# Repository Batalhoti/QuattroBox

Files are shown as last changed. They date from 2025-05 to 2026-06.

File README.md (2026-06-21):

# QuattroBox

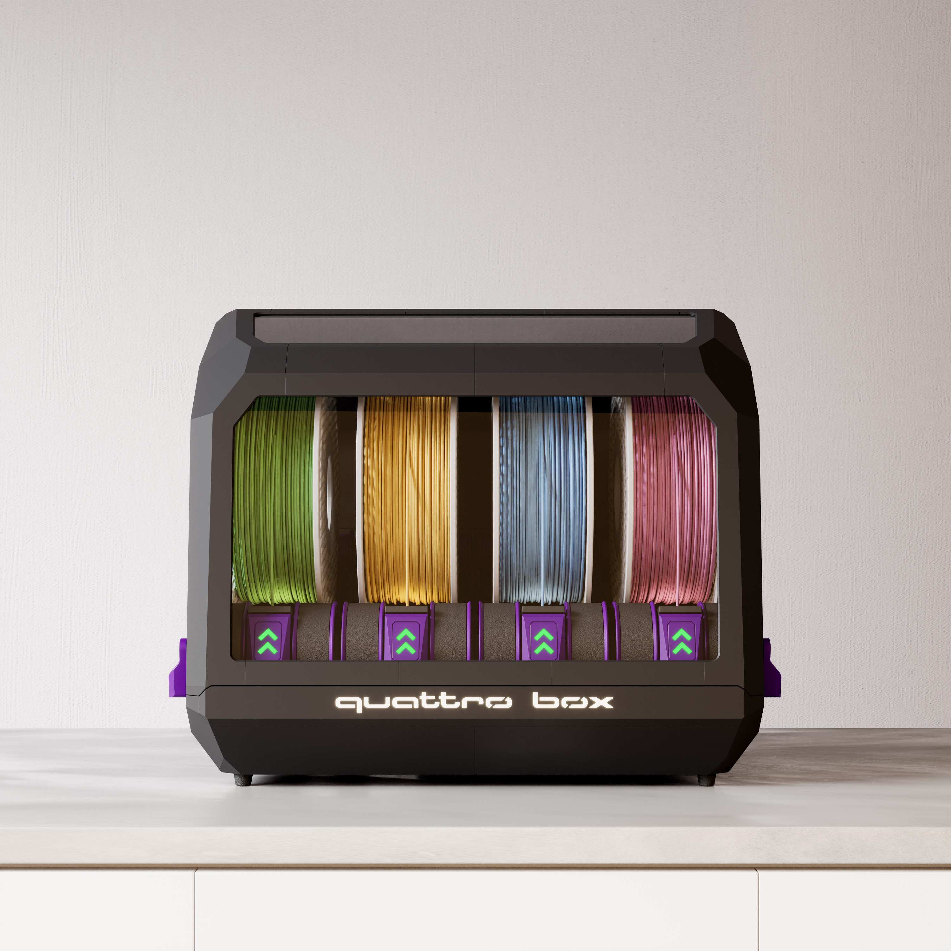
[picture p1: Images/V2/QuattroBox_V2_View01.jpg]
<p align="center">
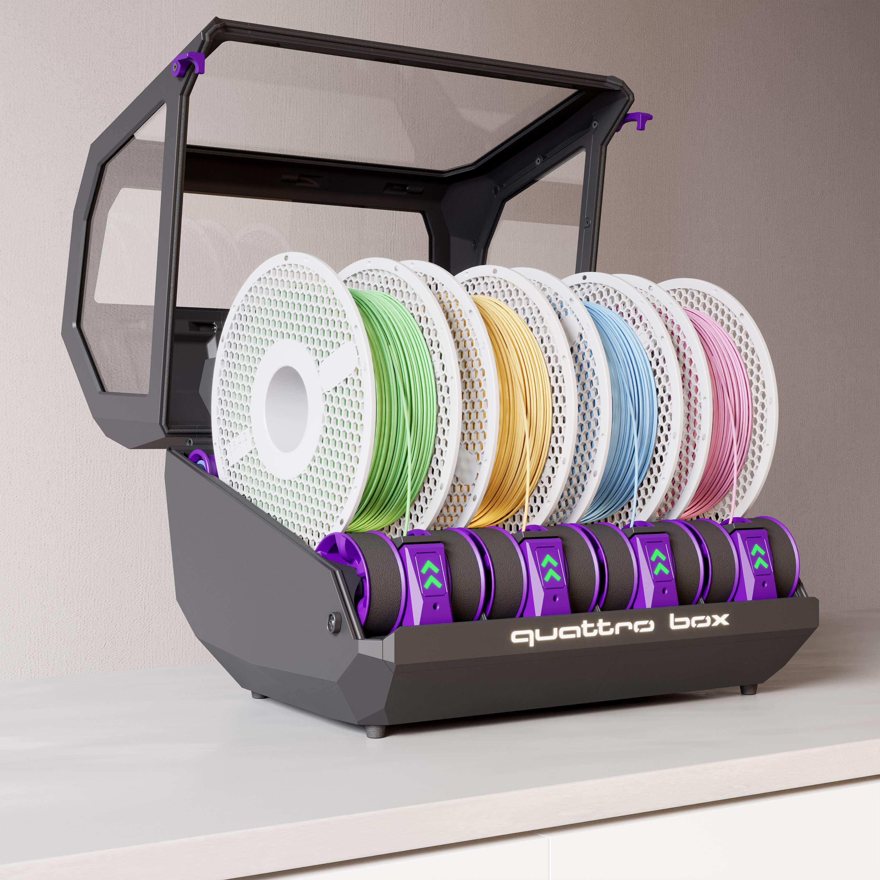
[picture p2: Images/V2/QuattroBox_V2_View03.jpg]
<p align="center">
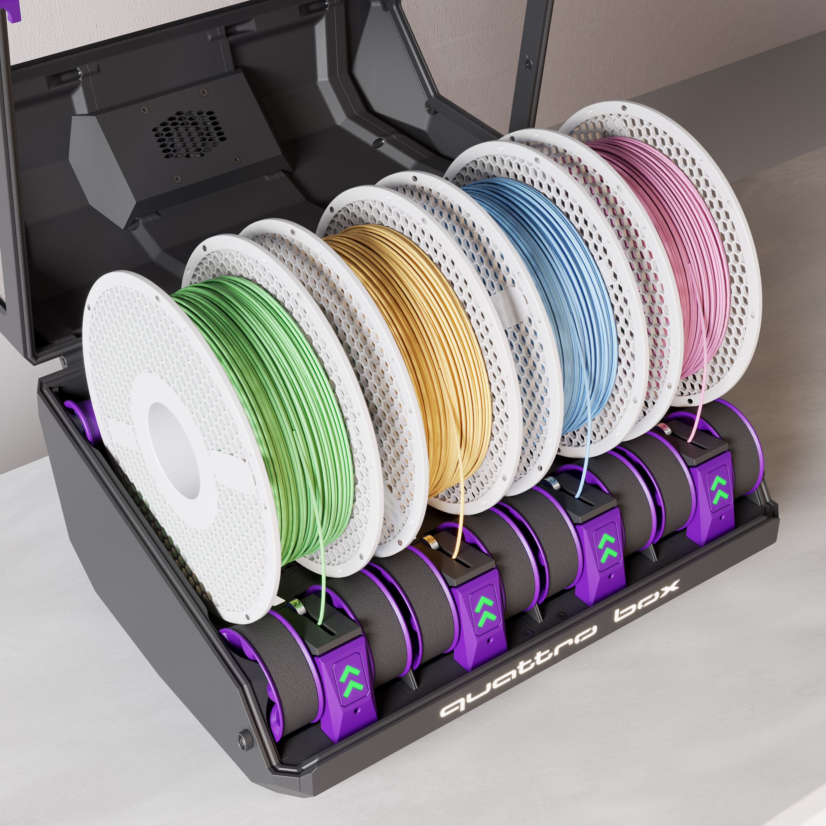
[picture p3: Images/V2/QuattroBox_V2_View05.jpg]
<p align="center">

## Description

QuattroBox v2 is the complete evolution of my MMU for 3D printers.
This version has been fully redesigned from the ground up, focusing on simplicity, compactness, and everyday usability.

I kept as much compatibility as possible with components from the previous version, while introducing significant improvements in both mechanical design and overall user experience.

## Key features
- Integrated filament dryer with AC heater
- Exhaust system for moisture removal
- Dedicated 4A power supply (optional)
- More compact extruder using a 23 mm NEMA17 (pancake)
- Hub with integrated Sync PSF
- Hinged lid (compatible with v1 panels)
- Magnetic bottom cover for easy access and maintenance
- Simplified and more organized assembly process
- All electronic components are assembled outside the enclosure before final installation
- Cable management clips
- Fully 3D printed structure (no aluminum extrusions required)
- Mounting supports to rest the MMU on the printer’s top extrusions
- Optimized for a 180 mm print area, with up to 142 mm height
- Compatible with [**Happy Hare**](https://github.com/moggieuk/Happy-Hare/wiki) for MMU control 

### Design and usability

The QuattroBox v2 design has also evolved significantly, not only in aesthetics but mainly in everyday usability. The status LED buttons are part of the system’s visual and functional identity, making it easy to quickly understand its operation. The system also features dedicated lighting to monitor the filament path. The internal layout has been reorganized to be cleaner and more intuitive, improving both assembly and maintenance. Access to components has also been designed to be simpler and more practical for day-to-day use.

### Design philosophy

QuattroBox v2 was designed to be accessible and easy to build, without compromising functionality.
The goal is to eliminate unnecessary complexity while maintaining a reliable and efficient multi-material system.  

##

I have a Discord channel on [HappyHare](https://discord.gg/pGSMCnBXc7), feel free to ask your questions and give suggestions

E se voce é brasileiro tenho um canal no servidor da [Orion 3D](https://discord.gg/Ap2ZFJXG7s)

## 

[BOM V2](https://docs.google.com/spreadsheets/d/1JrKG5omNthBb1Ab2Xag8QSc8Q7b502xr/edit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)

If you want to buy the complete kit

[SeleadLab v2 (Affiliate Link)](https://s.click.aliexpress.com/e/_c2JtqLK5)

[Trianglelab v2 (Affiliate Link)](https://s.click.aliexpress.com/e/_c4NRFI21)

## My build v1

[VIDEO 1](https://photos.app.goo.gl/y86quBDpxgd3wVg19)

[VIDEO 2](https://photos.app.goo.gl/qtu92ND3gbf3hNFr5)

<p align="center">
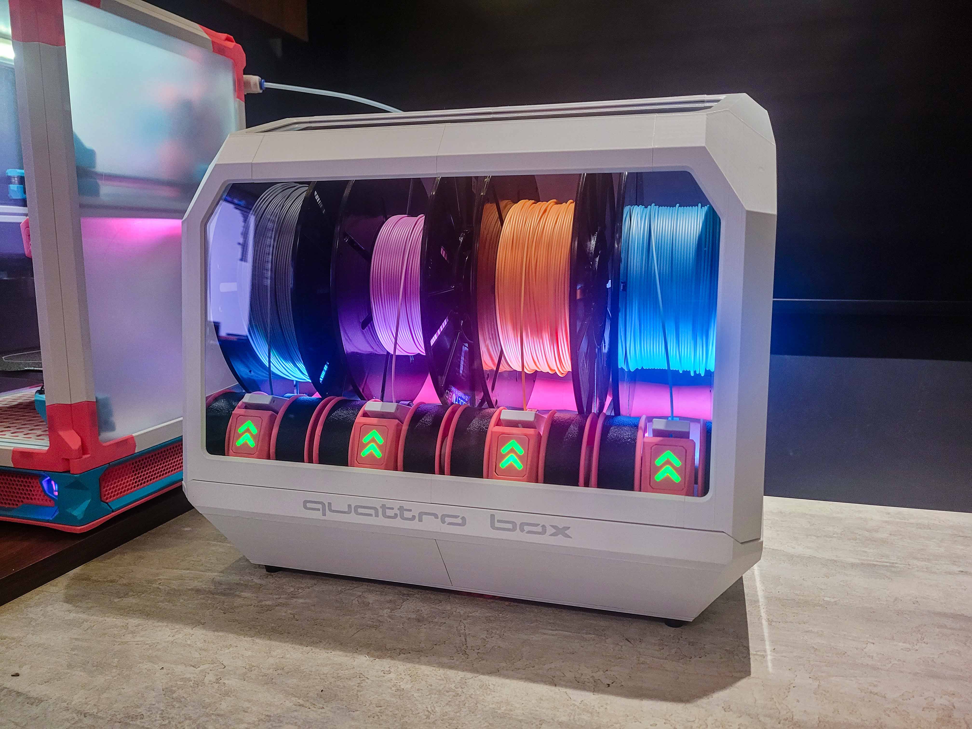
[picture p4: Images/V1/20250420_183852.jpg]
<p align="center">

## My build v2

Soon

## Acknowledgements

Special thanks to SkiBike for the [Filamentalist](https://github.com/Enraged-Rabbit-Community/ERCF_v2/tree/master/Recommended_Options/Filamentalist_Rewinder) design and to ArmoredTurtle for the [BoxTurtle](https://github.com/ArmoredTurtle/BoxTurtle) design, both of which inspired this project.
I also thank Diem who helped me with the publication here on GitHub

### [Change log](ChangeLog.md)

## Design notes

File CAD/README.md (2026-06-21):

To make the CAD model easier to navigate, the project is provided in two separate files:

### QuattroBox_V2_Assembly_up_to_180mm
Contains the larger parts split into multiple sections, allowing them to be printed on printers with a 180 mm or larger build area.

### QuattroBox_V2_Assembly_up_to_300mm

Contains the larger parts in fewer sections or as full-size parts, intended for printers with a 300 mm or larger build area.

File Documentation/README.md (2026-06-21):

I originally planned to create a step-by-step installation guide, but the release of Happy Hare V4 is approaching. For this reason, I am providing the configuration files that I currently use.

Please note that you will still need to verify and adjust the following parameters according to your setup:

- Toolhead sensor pins
- Cutter pins
- Toolhead sensor distances

It is recommended to review these settings before putting the system into operation.

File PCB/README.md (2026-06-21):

## PCBs
I am providing PCBs for the button and LED lane, making assembly easier for users who have little or no experience with wire soldering.

The PCB files are available for manufacturing. Ready-to-purchase versions are not yet available on AliExpress, but they are expected to be available soon.

### Button
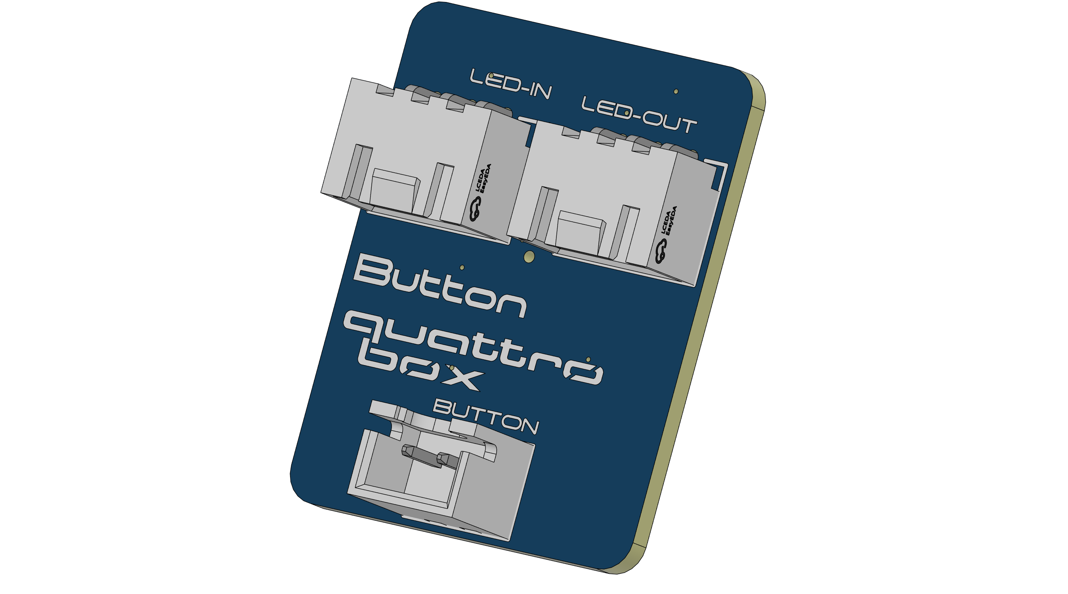
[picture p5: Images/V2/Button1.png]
<p align="center">

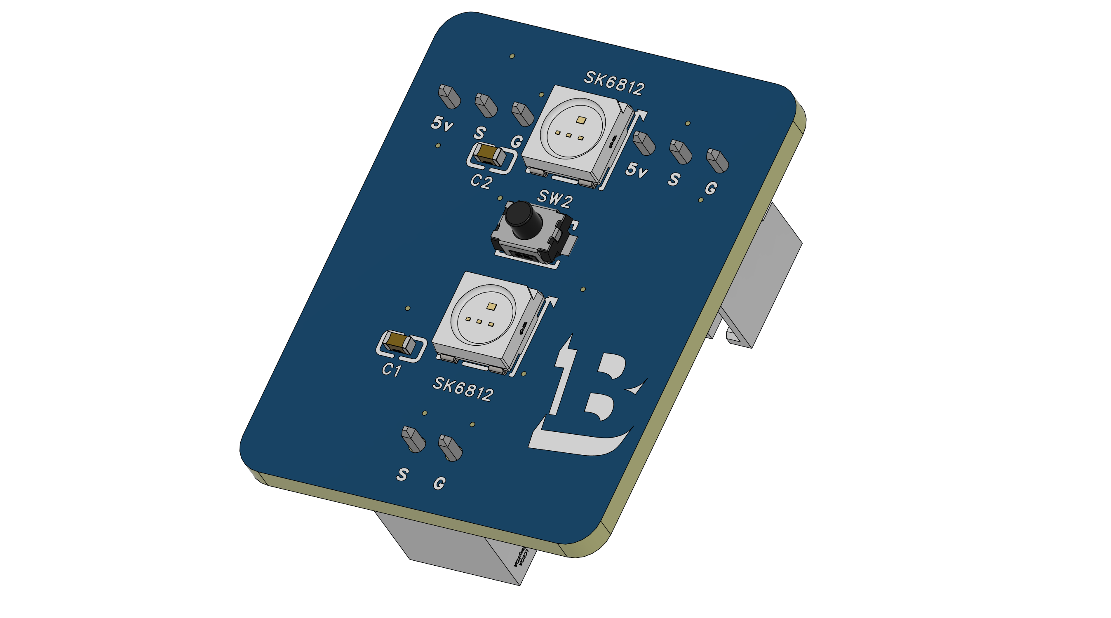
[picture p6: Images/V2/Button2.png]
<p align="center">

### LED Lane

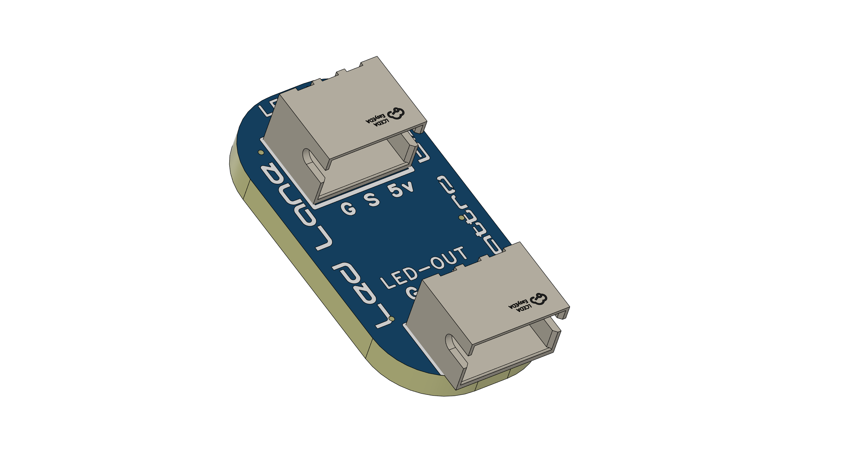
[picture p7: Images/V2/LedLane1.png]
<p align="center">

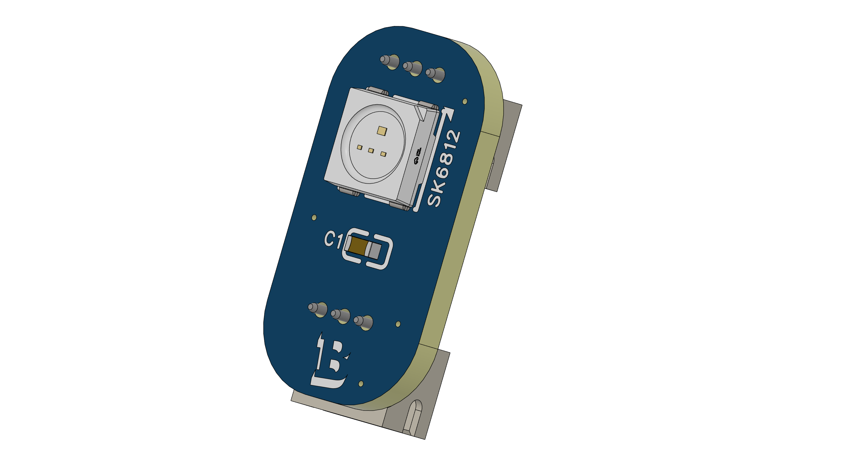
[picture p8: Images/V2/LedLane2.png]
<p align="center">

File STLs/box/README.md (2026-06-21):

### Box Single-Part 
For printers with a 400 mm or larger build volume.

### Box 2-Part 
For printers with a 300 mm or larger build volume.

### Box 8-Part 
For printers with a 180 mm or larger build volume.

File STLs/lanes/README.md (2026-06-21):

### base 1-Part 
For printers with a 300 mm or larger build volume.

### base 2-Part 
For printers with a 180 mm or larger build volume.

### PCBs Parts

If you are using the custom QuattroBox PCBs, also print the Button_PCB and LED_PCB parts

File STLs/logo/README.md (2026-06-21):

### Logo MMU
Printed as a single multicolor part and requires a printer equipped with an MMU system.
### Logo MMU 3-Part
A split version of the MMU logo designed for printers with smaller build volumes. Printed as three multicolor sections and assembled after printing. Requires an MMU system.

### Slicer MMU Logo
To print the Multi Color logo, adjust your slicer settings and enable the "Interface Shells" option under the Multimaterial section.

This setting helps improve the interface quality between different colors, resulting in a cleaner and more consistent finish.

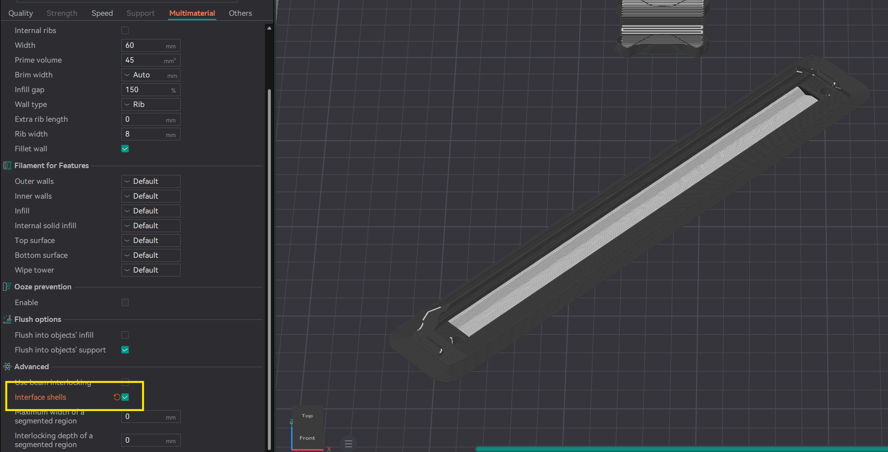
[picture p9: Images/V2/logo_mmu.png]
<p align="center">

### Logo Multi Part
Printed as separate colored parts that are assembled after printing. Does not require an MMU system.
### Logo Multi Part 3-Part
A split version of the Multi-Part logo designed for printers with smaller build volumes. Printed as three separate sections and assembled after printing. Does not require an MMU system!

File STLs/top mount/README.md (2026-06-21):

### Top Mount
For users with Voron printers that have non-standard dimensions, I am providing parametric files compatible with both the Voron and Monolith Panel standards.

Simply open the file in Fusion and modify the frame_size parameter, which represents the total outer length of the frame, measured on the outside and excluding the panels.
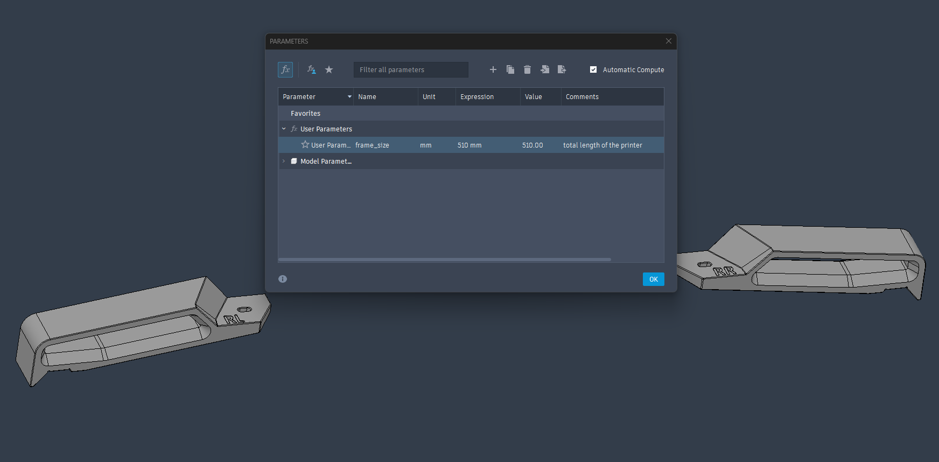
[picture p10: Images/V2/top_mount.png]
<p align="center">

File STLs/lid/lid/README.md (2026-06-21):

### Side 1-Part 
For printers with a 300 mm or larger build volume.

### Side 4-Part 
For printers with a 180 mm or larger build volume.

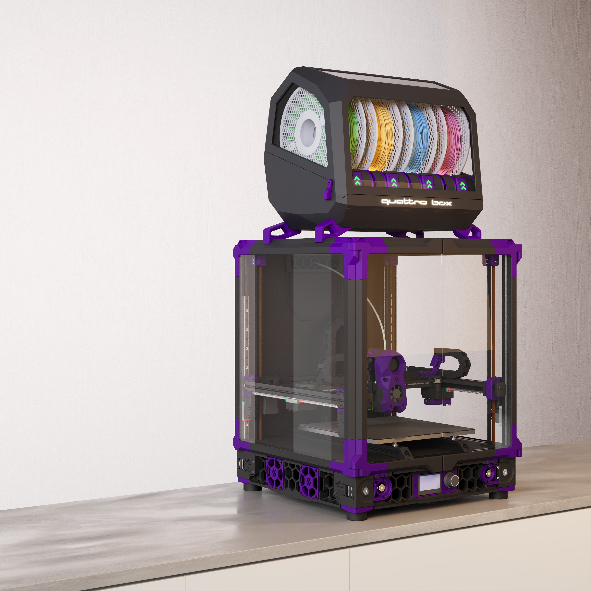
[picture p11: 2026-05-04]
Images/V2/QuattroBox_V2_V24_monolith_r1_View01.jpg

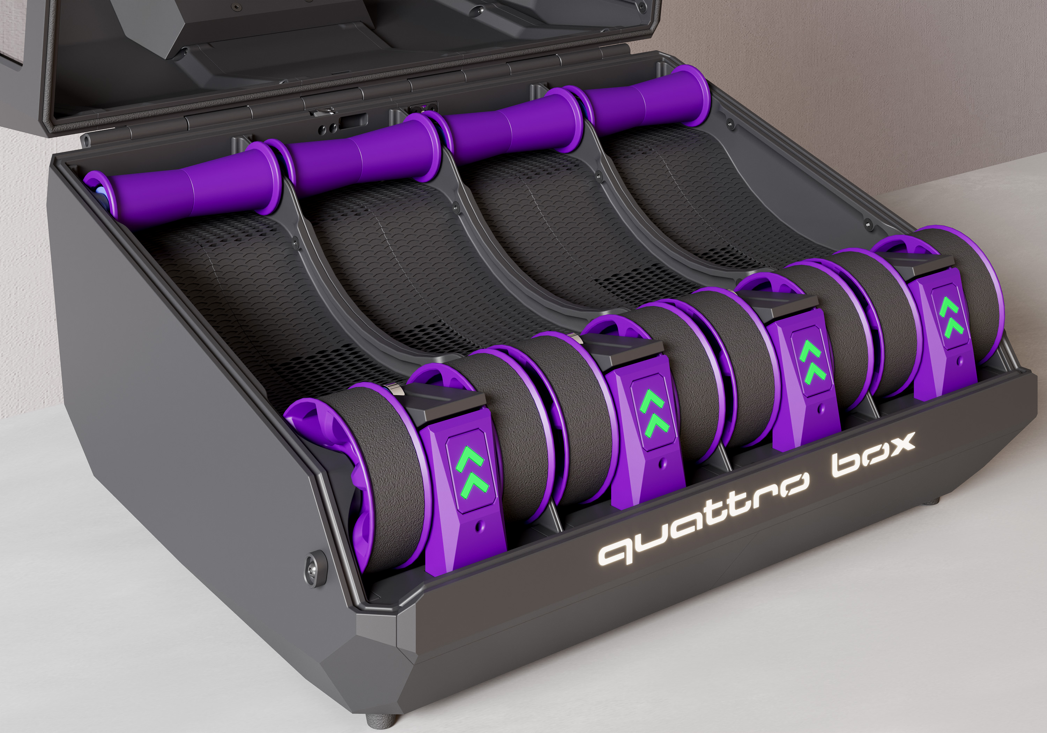
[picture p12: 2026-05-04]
Images/V2/QuattroBox_V2_View07.jpg

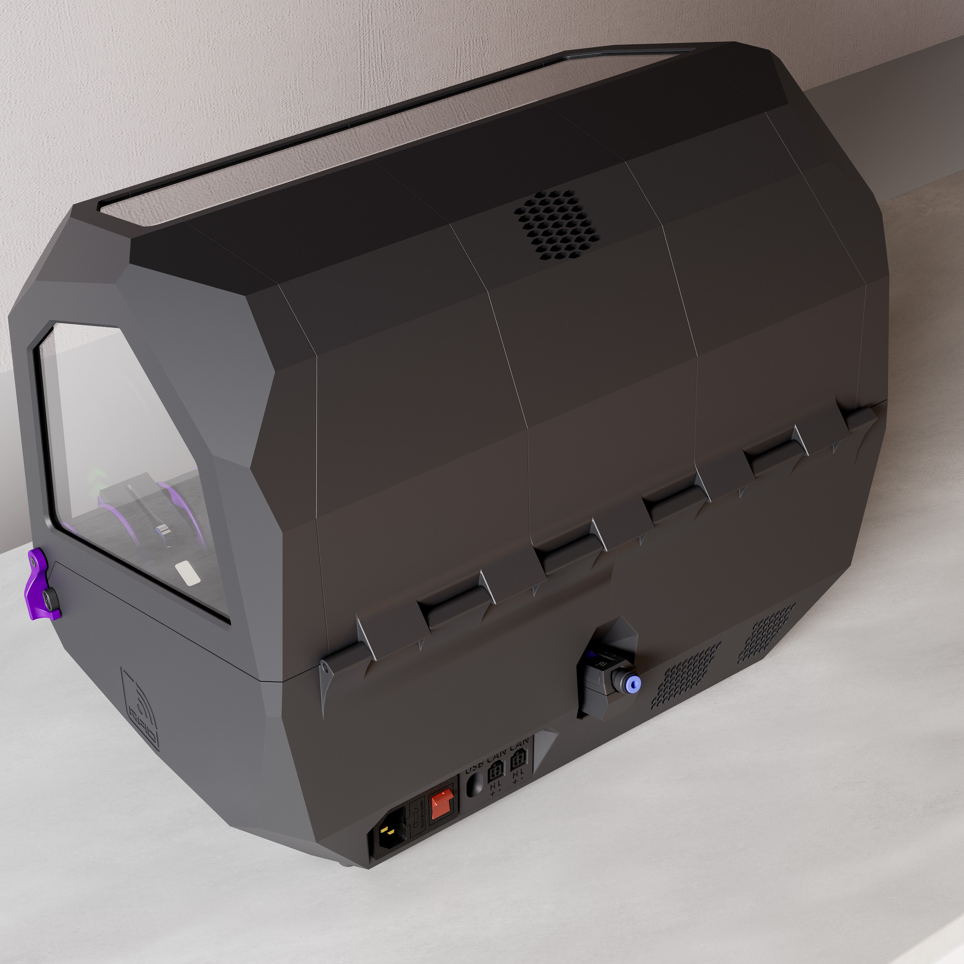
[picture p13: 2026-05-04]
Images/V2/QuattroBox_V2_View09.jpg

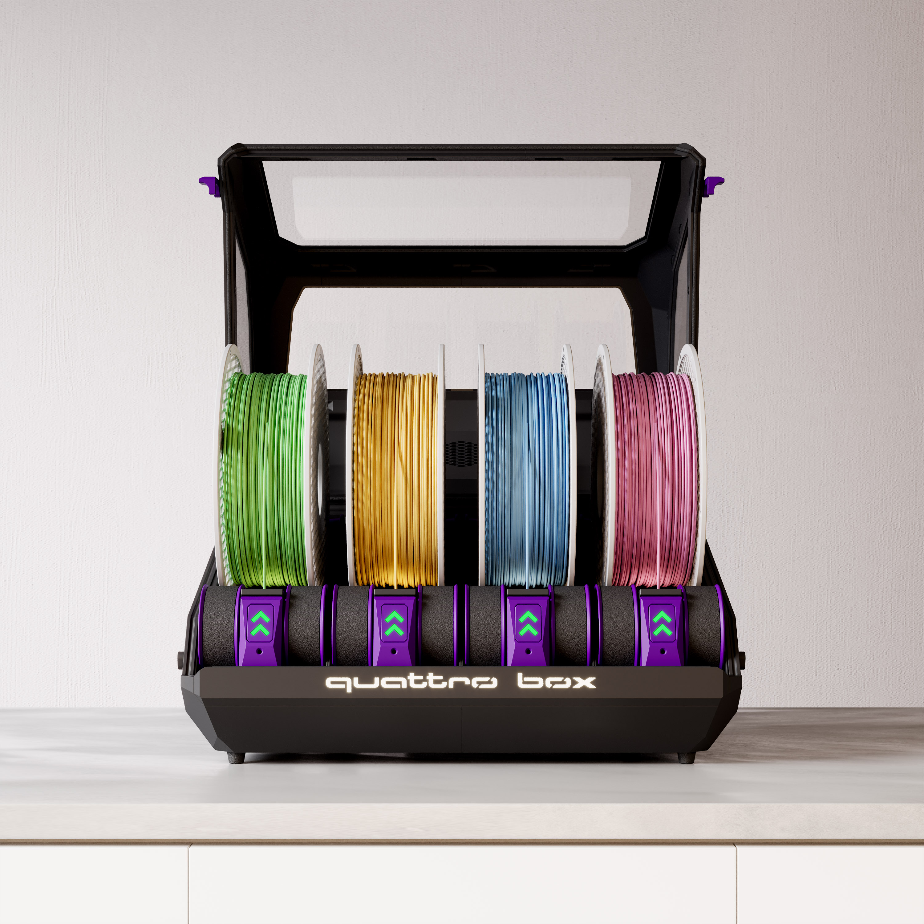
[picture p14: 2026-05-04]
Images/V2/QuattroBox_V2_View06.jpg

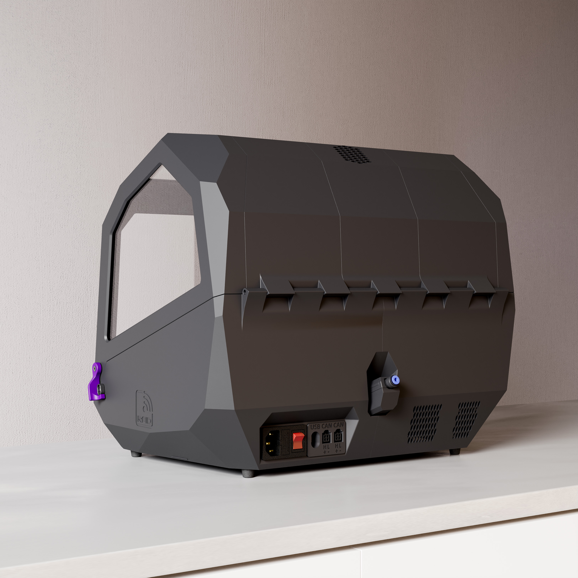
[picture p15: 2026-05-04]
Images/V2/QuattroBox_V2_View08.jpg

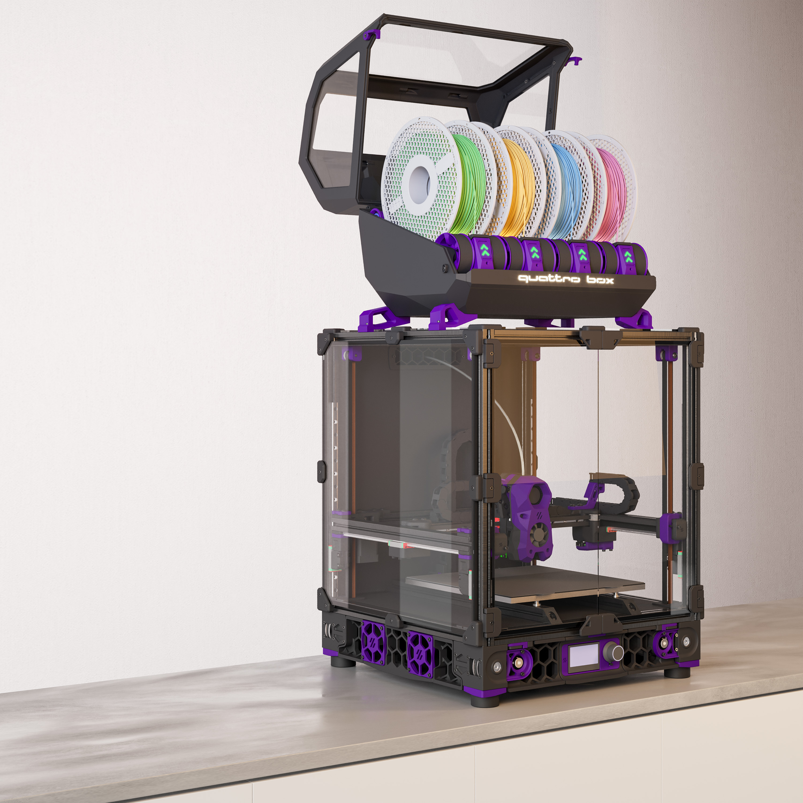
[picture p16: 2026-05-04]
Images/V2/QuattroBox_V2_V24_r1_View02.jpg

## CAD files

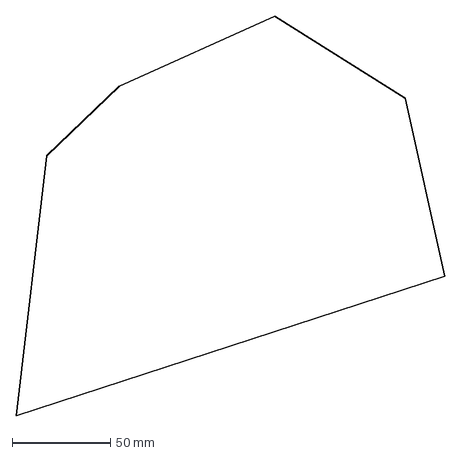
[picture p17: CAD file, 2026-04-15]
DXFs/2x_side_3mm.dxf
218.1 x 203.3 mm

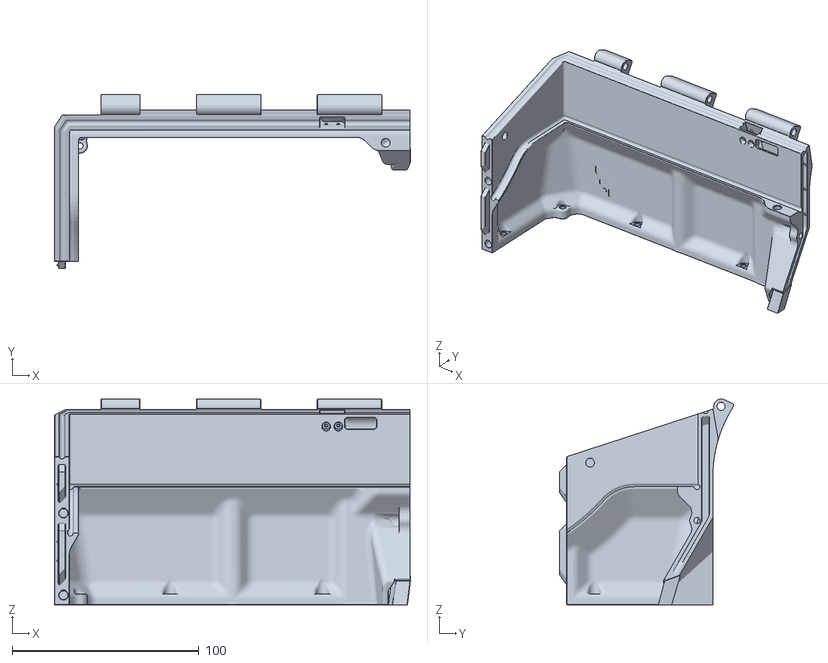
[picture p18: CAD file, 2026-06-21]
STLs/box/box_8_parts/box_left_rear_top.stl
190.9 x 93.6 x 110.4

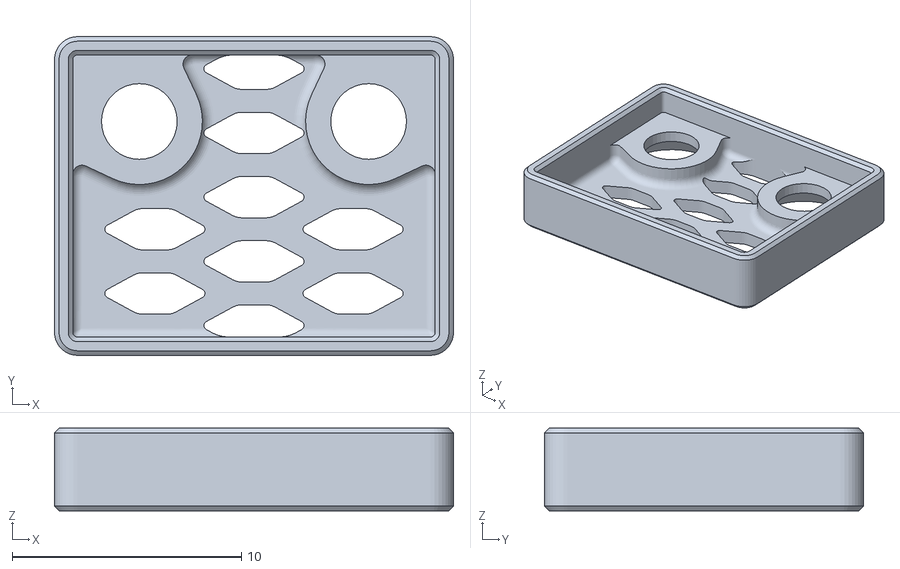
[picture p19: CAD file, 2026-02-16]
STLs/eletronics/BME_cover_x2.stl
17.4 x 13.9 x 3.60

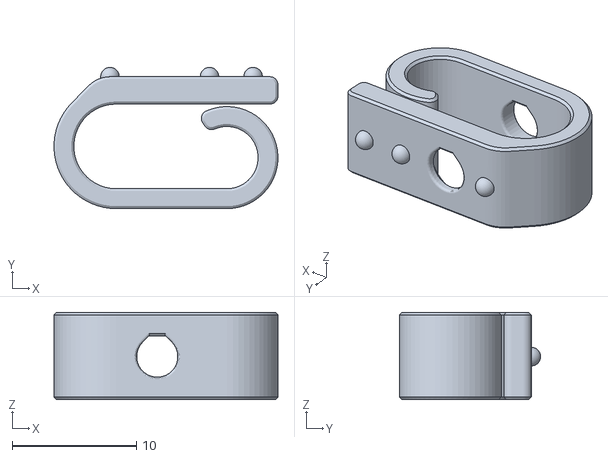
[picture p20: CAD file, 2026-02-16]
STLs/eletronics/cable clip/[a]_cable_clip_S_x28.stl
18.0 x 11.3 x 7.00

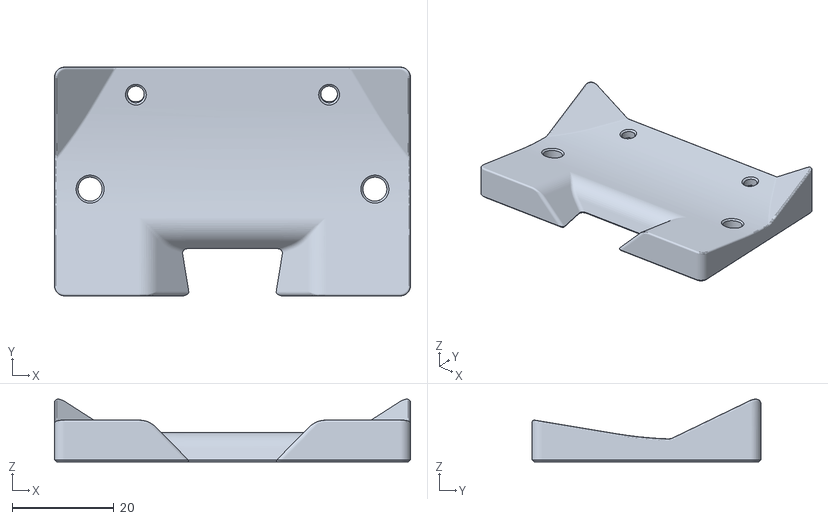
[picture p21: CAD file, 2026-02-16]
STLs/eletronics/chameleonX5/chameleonx5_pcb_mount.stl
70.0 x 45.0 x 12.3

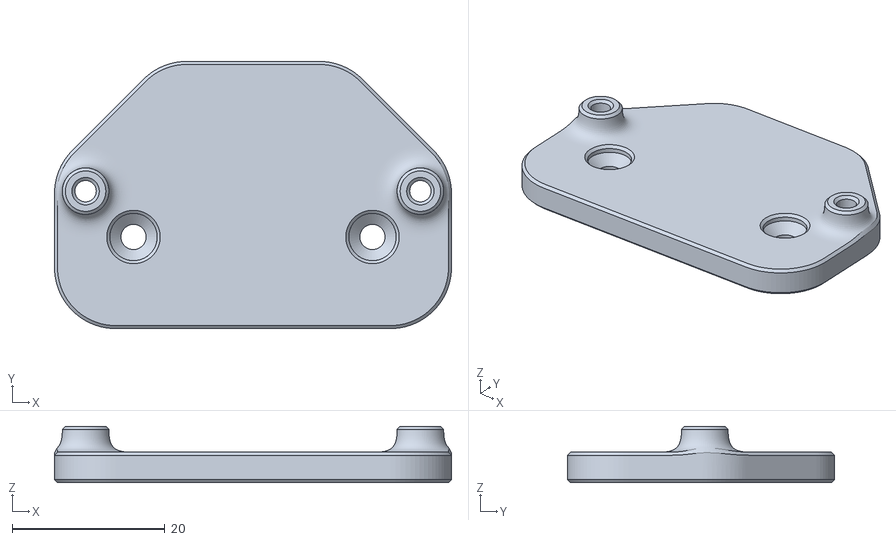
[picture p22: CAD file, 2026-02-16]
STLs/eletronics/discontinued/EBB36_mount.stl
52.0 x 35.0 x 7.40

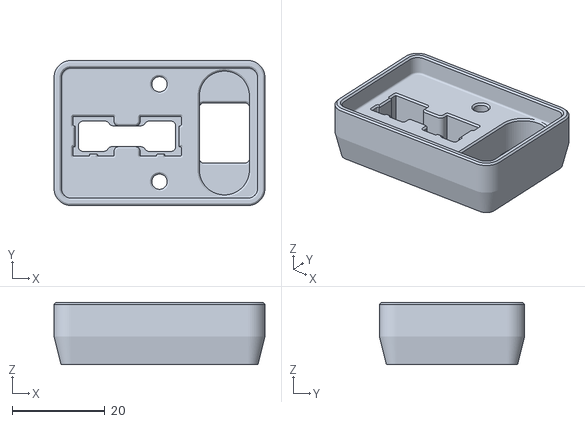
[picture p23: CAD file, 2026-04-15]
STLs/eletronics/inlet CAN USB/inlet_can_USB_B.stl
45.5 x 31.3 x 13.4

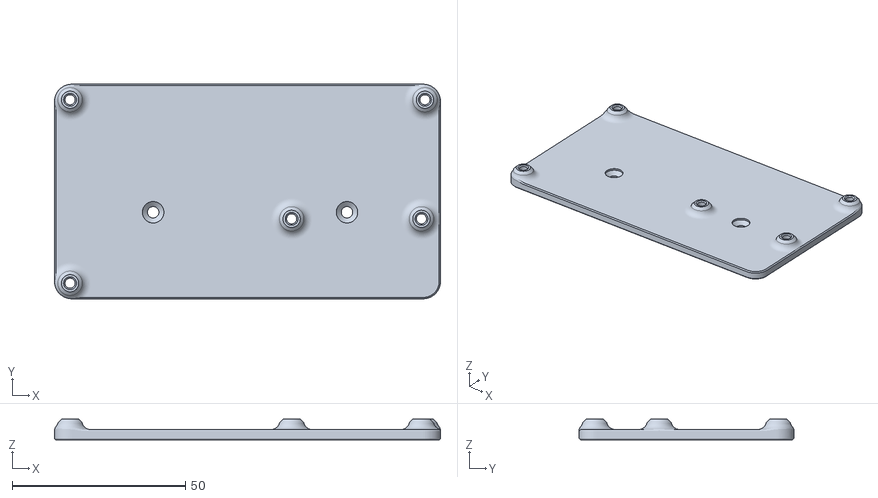
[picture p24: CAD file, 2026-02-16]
STLs/eletronics/MMBv2/MMBv2_mount.stl
111.5 x 62.0 x 6.00

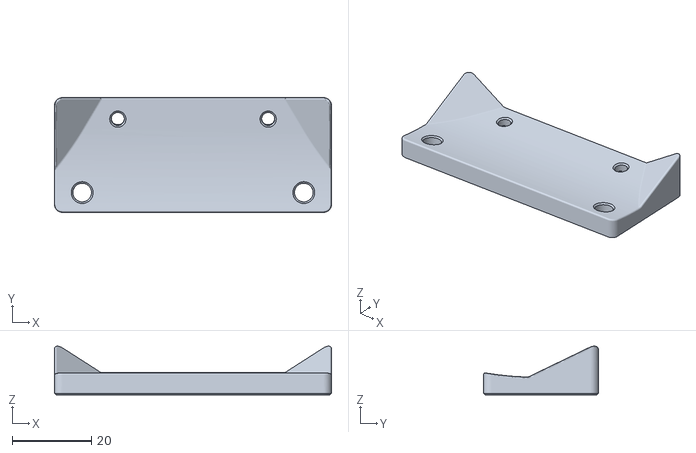
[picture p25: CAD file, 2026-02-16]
STLs/eletronics/wagos/wago_AC_mount.stl
70.0 x 29.0 x 12.3

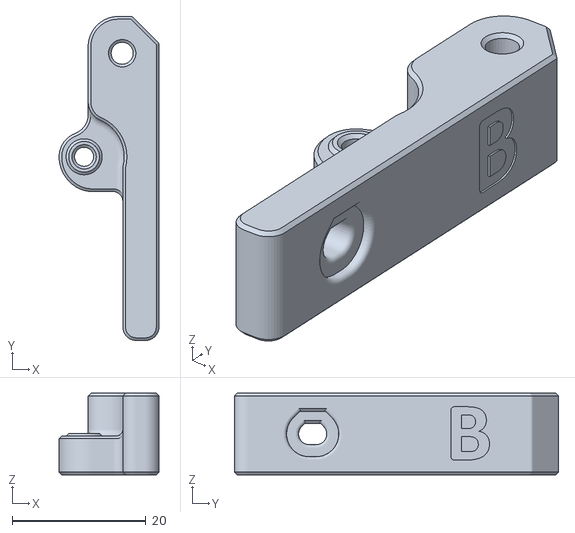
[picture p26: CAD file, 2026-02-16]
STLs/extruder/arm_extruder_B_x2.stl
15.0 x 48.5 x 12.2

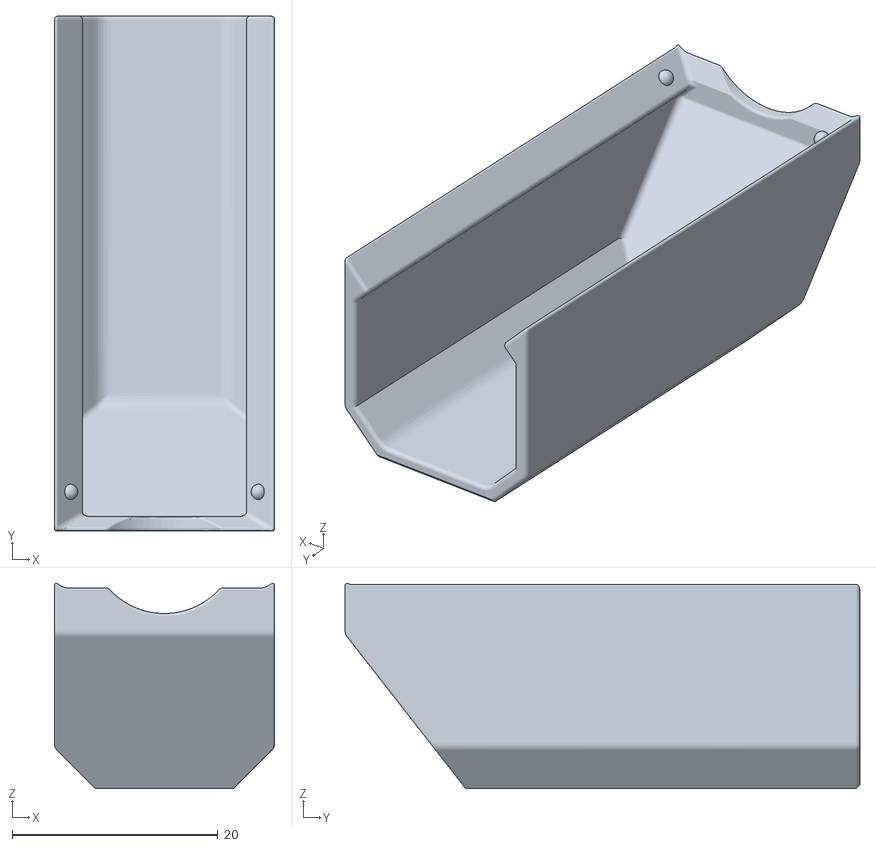
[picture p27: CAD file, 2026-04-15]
STLs/hub/cable_cover.stl
21.4 x 50.0 x 19.9

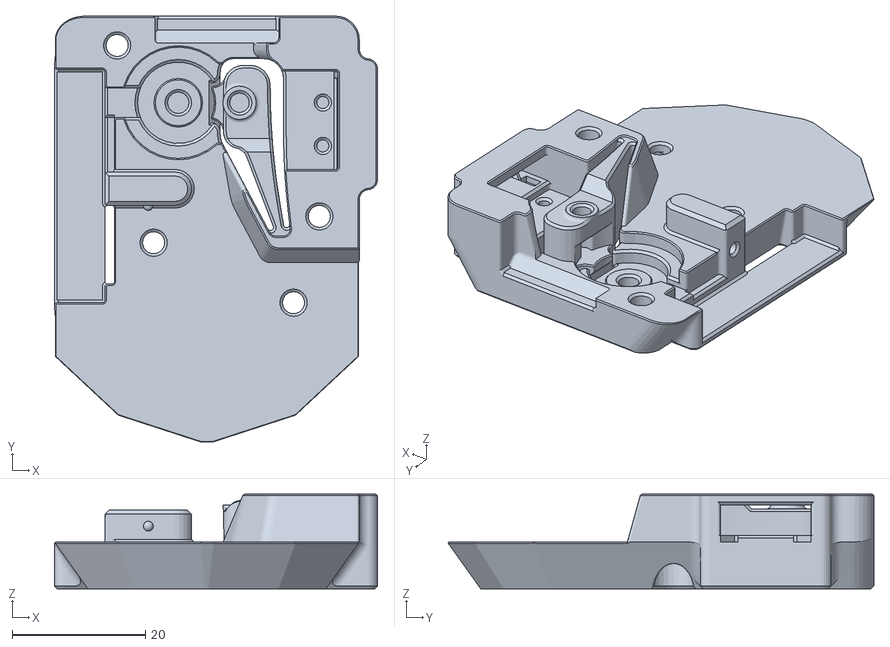
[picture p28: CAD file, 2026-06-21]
STLs/hub_psf/hub_A.stl
48.5 x 63.9 x 14.2

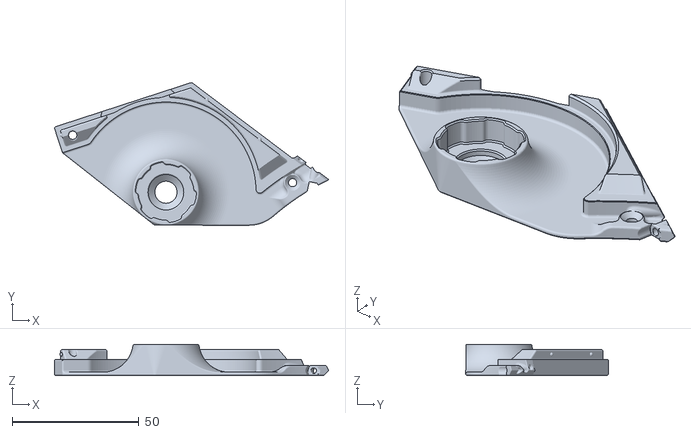
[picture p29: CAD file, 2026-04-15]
STLs/lanes/base_2_part/base_lane_0_1_2_right_2parts_front_x3.stl
107.9 x 56.1 x 12.4

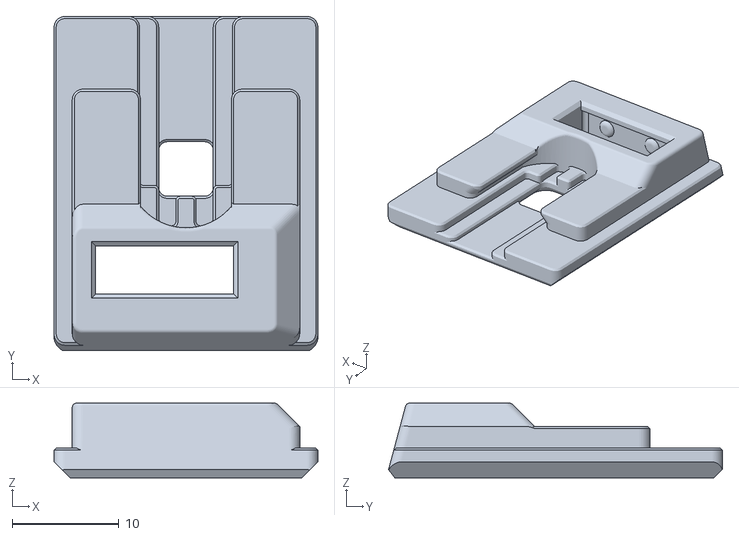
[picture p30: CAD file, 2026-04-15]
STLs/lanes/button/[o]_led_switch_mount_x4.stl
24.7 x 31.3 x 7.00

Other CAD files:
STLs/lanes/button_PCB/[a]_button_x4.stl
STLs/lanes/drive/center_drive_roller_x4.stl
STLs/lanes/idler/[a]_idler_roller_(female)_x4.stl
STLs/lanes/led/led_carrier_x4.stl
DXFs/1x_front_3mm.dxf
DXFs/1x_top_3mm.dxf
STLs/box/box_8_parts/box_left_front.stl
STLs/box/box_8_parts/box_left_rear_bottom.stl
STLs/box/box_8_parts/box_left_side.stl
STLs/box/box_8_parts/box_right_front.stl
STLs/box/box_8_parts/box_right_rear_bottom.stl
STLs/box/box_8_parts/box_right_rear_top.stl
STLs/box/box_8_parts/box_right_side.stl
STLs/eletronics/Inlet_lid.stl
STLs/eletronics/MMBv2/MMBv2_pcb_mount.stl
STLs/eletronics/cable clip/[a]_cable_clip_L_x11.stl
STLs/eletronics/cable clip/[a]_cable_clip_M_x3.stl
STLs/eletronics/chameleonX5/chameleonx5_mount.stl
STLs/eletronics/discontinued/RP2040_Oficial.stl
STLs/eletronics/discontinued/WagoMount_CAN.stl
STLs/eletronics/discontinued/WagoMount_DC.stl
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

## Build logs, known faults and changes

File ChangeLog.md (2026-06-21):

## Change log

### v2.0.2 - 06-20-2026

- Assembly manual.

- Calibration tool revision for version 2

- Added PCB for button and LED strip.

- Labels to identify the lid parts.

- Depth of the screws on the side lid 4 parts, thanks Atomique13.

- Expanded LED tensioner mount housing to fit the LED strip PCB.

- Adjustment of hub spring pressure.

- Added parametric top mount.

- Added servo tools.

- Small adjustments in the box, removed some cable clip slots.

- RFID support removed for now, will be added as an upgrade when ready.

- Spelling corrections of some part names.

- CAD update.

### v2.0.1 - 04-15-2026

- Tensioner arm improvements, the filament used to jam on it when the endless spool was activated.

- Adjustment to the central radius of the tensioner mount.

- Filename correction for the top mount files

### v2 - 04-15-2026

- Adjustment of hub cable cover dimensions.  

- Larger wire ducts on the cover.  

- Cover sides adapted for 180mm printers.  

- Mounting holes for the lanes in the box are now oval to facilitate assembly.  

- Heaters: improved AC wire routing, added a Wago connector for the fuse.  

- Removed from the official project the supports for EBB36, RP2040, Wago CAN bus, and Wago 24V; they will remain as extras for those who want to use them.  

- Adjustments to the LED carrier dimensions of the lanes.  

- Mounts for placing the MMU supported by the extrusions on top of the printer

- Box adjustments:  

  - Dimensions of the hub hole.  

  - Dimensions of the duct for exhaust and BME cables. 

  - Locations of cable clips.  

  - Dimensions of the hinge to use a 330mm iron rod. 

  - Spheres for fastening the top mount 

### v2 Beta - 02-16-2026

- Filament dryer with AC heater

- Exhaust fan to remove humid air

- Dedicated 4A power supply (optional, for those who prefer not to use the printer’s power)

- More compact extruder using a NEMA17 23mm (pancake) motor — other motor sizes will require modifications

- Hub with integrated Sync

- New Hub with Sync PSF

- Hinged lid

- Simplified assembly: all electronics are assembled outside the enclosure first, then installed into the case

- Cable management clips

- Optimized for a 180mm footprint with up to 142mm height

- Dedicated space for an RFID reader (still in development)

### v1.2.2.2 - 07-08-2025
- Manual corrections  
  - Heat insert from Filamentalist  
  - Warning about motor shaft dimensions on extruder without gearbox  
  - Screws for the hub with encoder  

### v1.2.2.1 - 06-28-2025
- Manual corrections  
  - Heatset Inserts  
  - Typo  
  - Button wire length  

### v1.2.2 - 06-22-2025
- Assembly manual added to support the build process  
- Updated buttons to avoid sharp edges on internal parts, improving fit and finish  
- Extruder updated with improved switch mounts for better triggering  
- Fixed incorrect label on the `Rear Left Top` part of the enclosure  
- Encoder adjusted to add more spring tension and tolerance, reducing print errors  
- Updated LED logo mount with a clear indicator for LED cable exit position  
- Revised cable channel for the LED logo wiring inside the box  
- Latch updated to use a 623 bearing for smoother operation  
- Added `axle_depth_tool` to assist with assembling the Filamentalis axle  
- Added `calibration_tool.stl` for tuning hole diameters and fits  
- Added `MR85 Insert` tool to help insert the MR85 bearing into the extruder  
- Updated `PTFE_Tools` for more precise PTFE tube cutting  

### v1.2.1 - 05-28-2025
- Support for mounting on the top of the printer with options for Monolith panel and Voron standard  

### v1.2 - 05-16-2025
- Extruders with 2 switches  
- 3 extruder options  
  - With BMG reduction, stepper nema 17  
  - With BMG reduction, stepper nema 14  
  - Without reduction, stepper nema 17 pancake  
- All extruders have a latch with an option to use a 623 bearing instead of the BMG idler  
- The Filamentalist wheel and base modified for 80mm shaft + M3 nuts  
- Added small plug between extruder and filamentalist  
- Right-side box modified for new connector  
- Connector for CAN bus (supports 2 buses) and USB  
- "Encoder" renamed to "Hub"  
- 2 hub options (with/without encoder)  
- Hub now uses MR63 bearing instead of 4mm ball  
- Added wire securing spots on the button  
- Logo uses heat inserts  
- Jig for cutting PTFE  
- Jig for soldering LED wires  
- Assembly tips  
- Updated BOM  
- Updated CAD  

### v1.1.1 - 04-20-2025
- Enclosure  

### v1.1 - 03-30-2025
- Extruder switch and encoder no longer need soldering (5-pin JST connector)  
- Improved ECAS encoder fitting  
- New design for Tensioner Arm  
- Button insertion order changed for better fit  
- Extra LED added on Tensioner Mount  
- Adjusted box supports  
- Text on Filamentalist bases  
- Change in MMB mounting method  
- Added MMB v2.0 mount  
- CAD updated  

### v1.01 - 03-09-2025
- Latch and Extruder Corrections  
  - Latch: new support, extended shaft lock  
  - Extruder: fitting for new latch, ECAS outlet improvements, extended shaft channel for nema 17  
- CAD updated  

### v1.0 - 01-30-2025
- New CAD file, redone in Fusion  
- New STLs (not compatible with old version)  
- Option to assemble with 623zz bearing instead of BMG  
- Box 8mm smaller  
- Box cover divided into 2 parts, compatible with 2 and 4-part box  
- 2 logo options (MMU printing or separate files)  
- Filamentalist parts and box with identifications  
- Button with hole for adjustment  
- All parts compatible with 255mm printers  

### v0.01 - 01-15-2025
- Update box (minor details, no need to reprint)  
- Box divided into 4 parts for printers <300mm  
- Update of 'tensioner_mount_load' with increased wire path  

### v0.1 - 01-13-2025
- Extruder update  
- Update CAD

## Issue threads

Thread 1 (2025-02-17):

BOM out of date

gufi, 2025-02-17:
BMG with screws -> Links to bmg but only 1 per customer, are there alternatives?
WS2812B 2.7MM LED Strip -> 404 not found
WS2812B RGBW neopixel LED -> 404 not found
D2F Switch and D2F-L Switch are the same link with different counts

BTT MMB doesn't have which drivers to buy so i assume any is acceptable for this setup?

Closed 2025-05-23.

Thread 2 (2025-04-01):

[a]_Encoder_top.stl comes with Encoder_Slotted_Wheel Embedded

mochoandre, 2025-04-01:
I printed Again the encoder, the new one, because I was having problems with readings in binky but looks there is an error in [a]_Encoder_top.stl  wich have the Encoder_Slotted_Wheel Embedded. Or it is meant to be a print in place?

Batalhoti, 2025-04-08:
There was an error in exporting the file, but it has already been corrected

Closed 2025-04-08.

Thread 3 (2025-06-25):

Missing heatset

Tance85, 2025-06-25:
On page 65 of the manual there is a missing heat set from that diagram. The missing heat set is in the over view though. Thanks for the amazing work.

Batalhoti, 2025-06-25:
Thanks, I hadn’t seen that, I'll fix it as soon as possible

Batalhoti, 2025-06-28:
Problem solved, thanks for the contribution.

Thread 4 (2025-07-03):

Spec Nema 17 extruder motor shaft too short

bryfixit, 2025-07-03:
I am using the spec motor NEMA 17 (17HS4023) for the extruder (no gearbox) and the shaft is about 5.70 mm too short to the end of the enclosure.  See photos for details

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

Batalhoti, 2025-07-05:
I’ve been using it this way here and haven’t had any issues.

**I’ll add a note about this in the manual!**

I’ll try to work on an update so the motor fits better, but I won’t set a deadline since I don’t have free time at the moment

Closed 2025-07-05.

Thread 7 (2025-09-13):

Wrong screw Hub with Encoder

scheini79, 2025-09-13:
There are two different dimensions for srews to fix the 623ZZ Bearing. In the drawing it's M3x8mm, while in the description it says M3x10.

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

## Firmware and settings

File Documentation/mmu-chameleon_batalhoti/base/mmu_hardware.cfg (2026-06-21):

########################################################################################################################
# Happy Hare MMU Software
#
# EDIT THIS FILE BASED ON YOUR SETUP
#
# Copyright (C) 2022-2025  moggieuk#6538 (discord)
#                          moggieuk@hotmail.com
# This file may be distributed under the terms of the GNU GPLv3 license.
#
# Goal: Happy Hare MMU hardware config file with config for MMB20 MCU board
#
# (\_/)
# ( *,*)
# (")_(") Happy Hare Ready
#
#
# Notes about setup of common external MCUs can be found here:
#  https://github.com/moggieuk/Happy-Hare/blob/main/doc/mcu_notes.md
# 
# Note about "touch" endstops: Happy Hare provides extremely flexible homing options using both single steppers or
# synced steppers. The "touch" option leverages stallguard and thus requires the appropriate 'diag_pin' and stallguard
# parameters set on the TMC driver section. If you have the diag_pin exposed, it is harmless to define this because
# they will only be used when explicitly needed and configured.
#
# Touch option for each stepper provides these benefits / possibilities (experimental):
#  - on extruder stepper allows for the automatic detection of the nozzle!
#  - on selector stepper allows for the automatic detection of filament stuck in the gate and subsequent recovery
#  - on gear stepper allows for the automatic detection of the extruder entrance
#
# In summary, "touch" homing with your MMU is an advanced option that requires patience and careful tuning. Everything
# works with regular endstops and there are workaround options for certain homing points (like extruder entry) in
# the absence of any endstop. I'm really interested in creative setups. Ping me on Discord (moggieuk#6538)
#
# See 'mmu.cfg' for serial definition and pins aliases
#
# HOMING CAPABLE EXTRUDER (VERY ADVANCED) -----------------------------------------------------------------------------
# With Happy Hare installed even the extruder can be homed. You will find the usual 'endstop' parameters can be added
# to your '[extruder]' section.  Useless you have some clever load cell attached to your nozzle it only really makes
# sense to configure stallguard style "touch" homing. To do this add lines similar to this to your existing
# '[extruder]' definition in printer.cfg.
#
#    [extruder]
#    endstop_pin: tmc2209_extruder:virtual_endstop
#
# Also be sure to add the appropriate stallguard config to the TMC section, e.g.
#
#    [tmc2209 extruder]
#    diag_pin: E_DIAG		# Set to MCU pin connected to TMC DIAG pin for extruder
#    driver_SGTHRS: 100		# 255 is most sensitive value, 0 is least sensitive
#
# Happy Hare will take care of the rest and add a 'mmu_ext_touch' endstop automatically
#


# MMU MACHINE / TYPE ---------------------------------------------------------------------------------------------------
# ███╗   ███╗███╗   ███╗██╗   ██╗    ███╗   ███╗ █████╗  ██████╗██╗  ██╗██╗███╗   ██╗███████╗
# ████╗ ████║████╗ ████║██║   ██║    ████╗ ████║██╔══██╗██╔════╝██║  ██║██║████╗  ██║██╔════╝
# ██╔████╔██║██╔████╔██║██║   ██║    ██╔████╔██║███████║██║     ███████║██║██╔██╗ ██║█████╗  
# ██║╚██╔╝██║██║╚██╔╝██║██║   ██║    ██║╚██╔╝██║██╔══██║██║     ██╔══██║██║██║╚██╗██║██╔══╝  
# ██║ ╚═╝ ██║██║ ╚═╝ ██║╚██████╔╝    ██║ ╚═╝ ██║██║  ██║╚██████╗██║  ██║██║██║ ╚████║███████╗
# ╚═╝     ╚═╝╚═╝     ╚═╝ ╚═════╝     ╚═╝     ╚═╝╚═╝  ╚═╝ ╚═════╝╚═╝  ╚═╝╚═╝╚═╝  ╚═══╝╚══════╝
[mmu_machine]

# Number of selectable gate on (each) MMU. Generally this is a single number, but with multi-mmu (type-B) setups
# it can be a comma separated list of the number of gates per unit.
# E.g. 'num_gates: 4,4,2' for a 2xBox Turtle and 1xNight Owl multiplexed setup
#
num_gates: 4

# MMU Vendor & Version is used to automatically configure some parameters and validate configuration
# If custom set to "Other" and uncomment the additional parameters below
#
# ERCF          1.1  add "s" suffix for Springy, "b" for Binky, "t" for Triple-Decky
#                    e.g. "1.1sb" for v1.1 with Springy mod and Binky encoder
# ERCF          2.0  community edition ERCFv2
# ERCF          2.5
# Tradrack      1.0  add "e" if encoder is fitted (assumed to be Binky)
# AngryBeaver   1.0
# BoxTurtle     1.0
# NightOwl      1.0
# 3MS           1.0
# 3D Chameleon  1.0
# Pico          1.0
# Prusa         3.0  NOT YET SUPPORTED - COMING SOON
# Other              Generic setup that may require further customization of 'cad' parameters. See doc in mmu_parameters.cfg
#
mmu_vendor: QuattroBox			# MMU family
mmu_version: 1.0			# MMU hardware version number (add mod suffix documented above)

# The following attributes are set internally from vendor/version above. Only uncomment to customize the vendor
# default or for custom ("Other") designs
#
#selector_type: VirtualSelector		# E.g. LinearSelector (type-A), VirtualSelector (type-B), MacroSelector, RotarySelector, ...
#variable_bowden_lengths: 0		# 1 = If MMU design has different bowden lengths per gate, 0 = bowden length is the same
#variable_rotation_distances: 1		# 1 = If MMU design has dissimilar drive/BMG gears, thus rotation distance, 0 = One drive gear (e.g. Tradrack)
#require_bowden_move: 1			# 1 = If MMU design has bowden move that is included in load/unload, 0 = zero length bowden (skip bowden move)
#filament_always_gripped: 1		# 1 = Filament is always trapped by MMU (most type-B designs), 0 = MMU can release filament
#has_bypass: 0				# 1 = Bypass gate available, 0 = No filament bypass possible

# Uncomment to change the display name in UI's.  Defaults to the vendor name
#display_name: My Precious

# Fullname of environment sensor for MMU filament storage (displays temp and humidity in UI)
# Polls for "temperature" and "humidity"
# E.g. If you have a section like this: [temperature_sensor MMU_enclosure]
# Set: environment_sensor: temperature_sensor MMU_enclosure
environment_sensor: temperature_sensor MMU_Chamber

filament_heater: heater_generic MMU_heater

homing_extruder: 1			# CAUTION: Normally this should be 1. 0 will disable the homing extruder capability


# FILAMENT DRIVE GEAR STEPPER(S)  --------------------------------------------------------------------------------------
#  ██████╗ ███████╗ █████╗ ██████╗ 
# ██╔════╝ ██╔════╝██╔══██╗██╔══██╗
# ██║  ███╗█████╗  ███████║██████╔╝
# ██║   ██║██╔══╝  ██╔══██║██╔══██╗
# ╚██████╔╝███████╗██║  ██║██║  ██║
#  ╚═════╝ ╚══════╝╚═╝  ╚═╝╚═╝  ╚═╝
# Note that 'toolhead' & 'mmu_gear' endstops will automatically be added if a toolhead sensor or gate sensor is defined
#
# The default values are tested with the ERCF BOM NEMA14 motor. Please adapt these values to the motor you are using
# Example : for NEMA17 motors, you'll usually use higher current
#
[tmc2209 stepper_mmu_gear]
uart_pin: mmu:MMU_GEAR_UART
run_current: 0.9			# ERCF BOM NEMA14 motor
hold_current: 0.2			# Recommend to be small if not using "touch" or move (TMC stallguard)
interpolate: True
sense_resistor: 0.110			# Usually 0.11, 0.15 for BTT TMC2226
stealthchop_threshold: 0		# Spreadcycle has more torque and better at speed
#
# Uncomment two lines below if you have TMC and want the ability to use filament "touch" homing with gear stepper
#diag_pin: ^mmu:MMU_GEAR_DIAG		# Set to MCU pin connected to TMC DIAG pin for gear stepper
#driver_SGTHRS: 60			# 255 is most sensitive value, 0 is least sensitive

[stepper_mmu_gear]
step_pin: mmu:MMU_GEAR_STEP
dir_pin: mmu:MMU_GEAR_DIR
enable_pin: !mmu:MMU_GEAR_ENABLE
rotation_distance: 22.7316868		# Bondtech 5mm Drive Gears. Overridden by 'mmu_gear_rotation_distance' in mmu_vars.cfg
gear_ratio: 1:1			# E.g. ERCF 80:20, Tradrack 50:17
microsteps: 16 				# Recommend 16. Increase only if you "step compress" issues when syncing
full_steps_per_rotation: 200		# 200 for 1.8 degree, 400 for 0.9 degree
#
# Uncomment the two lines below to enable filament "touch" homing option with gear motor
#extra_endstop_pins: tmc2209_stepper_mmu_gear:virtual_endstop
#extra_endstop_names: mmu_gear_touch

# ADDITIONAL FILAMENT DRIVE GEAR STEPPERS FOR TYPE-B MMU's -------------------------------------------------------------
# Note that common parameters are inherited from base stepper_mmu_gear, but can be uniquely specified here too
#
# Filament Drive Gear_1 --------------------------
[tmc2209 stepper_mmu_gear_1]
uart_pin: mmu:MMU_GEAR_UART_1

[stepper_mmu_gear_1]
step_pin: mmu:MMU_GEAR_STEP_1
dir_pin: mmu:MMU_GEAR_DIR_1
enable_pin: !mmu:MMU_GEAR_ENABLE_1

# Filament Drive Gear_2 --------------------------
[tmc2209 stepper_mmu_gear_2]
uart_pin: mmu:MMU_GEAR_UART_2

[stepper_mmu_gear_2]
step_pin: mmu:MMU_GEAR_STEP_2
dir_pin: !mmu:MMU_GEAR_DIR_2
enable_pin: !mmu:MMU_GEAR_ENABLE_2

# Filament Drive Gear_3 --------------------------
[tmc2209 stepper_mmu_gear_3]
uart_pin: mmu:MMU_GEAR_UART_3

[stepper_mmu_gear_3]
step_pin: mmu:MMU_GEAR_STEP_3
dir_pin: !mmu:MMU_GEAR_DIR_3
enable_pin: !mmu:MMU_GEAR_ENABLE_3
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

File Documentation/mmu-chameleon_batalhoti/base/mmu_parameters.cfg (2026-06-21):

########################################################################################################################
# Happy Hare MMU Software
#
# Template file for MMU's with Virtual Selector (Type-B designs like Box Turtle, Night Owl, Angry Beaver, ...)
# This file omits selector and selector-servo configuration and a few other options that don't make sense
#
# EDIT THIS FILE BASED ON YOUR SETUP
#
# Copyright (C) 2022-2026  moggieuk#6538 (discord)
#                          moggieuk@hotmail.com
# This file may be distributed under the terms of the GNU GPLv3 license.
#
# Goal: Main configuration parameters for the klipper module
#
# (\_/)
# ( *,*)
# (")_(") Happy Hare Ready
#
# Notes:
#   Macro configuration is specified separately in 'mmu_macro_vars.cfg'.
#   Full details in https://github.com/moggieuk/Happy-Hare/tree/main/doc/configuration.md
#
[mmu]
happy_hare_version: 3.42			# Don't mess, used for upgrade detection

# MMU Hardware Limits --------------------------------------------------------------------------------------------------
# ██╗     ██╗███╗   ███╗██╗████████╗███████╗
# ██║     ██║████╗ ████║██║╚══██╔══╝██╔════╝
# ██║     ██║██╔████╔██║██║   ██║   ███████╗
# ██║     ██║██║╚██╔╝██║██║   ██║   ╚════██║
# ███████╗██║██║ ╚═╝ ██║██║   ██║   ███████║
# ╚══════╝╚═╝╚═╝     ╚═╝╚═╝   ╚═╝   ╚══════╝
#
# Define the physical limits of your MMU. These settings will be respected regardless of individual speed settings.
#
gear_max_velocity: 1000			# Never to be exceeded gear velocity regardless of specific parameters
gear_max_accel: 1500			# Never to be exceeded gear acceleration regardless of specific parameters


# Logging --------------------------------------------------------------------------------------------------------------
# ██╗      ██████╗  ██████╗  ██████╗ ██╗███╗   ██╗ ██████╗ 
# ██║     ██╔═══██╗██╔════╝ ██╔════╝ ██║████╗  ██║██╔════╝ 
# ██║     ██║   ██║██║  ███╗██║  ███╗██║██╔██╗ ██║██║  ███╗
# ██║     ██║   ██║██║   ██║██║   ██║██║██║╚██╗██║██║   ██║
# ███████╗╚██████╔╝╚██████╔╝╚██████╔╝██║██║ ╚████║╚██████╔╝
# ╚══════╝ ╚═════╝  ╚═════╝  ╚═════╝ ╚═╝╚═╝  ╚═══╝ ╚═════╝ 
#
# log_level & logfile_level can be set to one of (0 = essential, 1 = info, 2 = debug, 3 = trace, 4 = stepper moves)
# Generally you can keep console logging to a minimal whilst still sending debug output to the mmu.log file
# Increasing the console log level is only really useful during initial setup to save having to constantly open the log file
# Note: that it is not recommended to keep logging at level greater that 2 (debug) if not debugging an issue because
# of the additional overhead
#
log_level: 1
log_file_level: 2			# Can also be set to -1 to disable log file completely
log_statistics: 1 			# 1 to log statistics on every toolchange (default), 0 to disable (but still recorded)
log_visual: 1				# 1 log visual representation of filament, 0 = disable
log_startup_status: 1			# Whether to log tool to gate status on startup, 1 = summary (default), 0 = disable
log_m117_messages: 1			# Whether send toolchange message via M117 to screen


# Movement speeds ------------------------------------------------------------------------------------------------------
# ███████╗██████╗ ███████╗███████╗██████╗ ███████╗
# ██╔════╝██╔══██╗██╔════╝██╔════╝██╔══██╗██╔════╝
# ███████╗██████╔╝█████╗  █████╗  ██║  ██║███████╗
# ╚════██║██╔═══╝ ██╔══╝  ██╔══╝  ██║  ██║╚════██║
# ███████║██║     ███████╗███████╗██████╔╝███████║
# ╚══════╝╚═╝     ╚══════╝╚══════╝╚═════╝ ╚══════╝
#
# Long moves are faster than the small ones and used for the bulk of the bowden movement. You can set two fast load speeds
# depending on whether pulling from the spool or filament buffer (if fitted and not the first time load). This can be helpful
# in allowing faster loading from buffer and slower when pulling from the spool because of the additional friction (prevents
# loosing steps). Unloading speed can be tuning if you have a rewinder system that imposes additional limits.
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

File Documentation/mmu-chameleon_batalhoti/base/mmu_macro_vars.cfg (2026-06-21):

########################################################################################################################
# Happy Hare MMU Software
#
# EDIT THIS FILE BASED ON YOUR SETUP
#
# Copyright (C) 2022-2026  moggieuk#6538 (discord)
#                          moggieuk@hotmail.com
# This file may be distributed under the terms of the GNU GPLv3 license.
#
# Goal: Happy Hare supporting MACRO configuration
#
# (\_/)
# ( *,*)
# (")_(") Happy Hare Ready
#
#
# Supporting set of macros supplied with Happy Hare can be customized by editing the macro "variables" declared here.
#
# This configuration will automatically retained and upgraded between releases (a backup of previous config files will
# always be made for your reference). If you want to customize macros beyond what is possible through these variables
# it is highly recommended you copy the macro to a new name and change the callback macro name in 'mmu_parameters.cfg'
# That way the default macros can still be upgraded but your customization will be left intact
#


# PERSISTED STATE ---------------------------------------------------------
# Happy Hare stores configuration and state in the klipper variables file.
# Since klipper can only be a single 'save_variables' file, if you already
# have one you will need to merge the two and point this appropriately.
#
[save_variables]
filename: ~/printer_data/config/mmu/mmu_vars.cfg


# NECESSARY KLIPPER OVERRIDES ---------------------------------------------
# ██╗  ██╗██╗     ██╗██████╗ ██████╗ ███████╗██████╗ 
# ██║ ██╔╝██║     ██║██╔══██╗██╔══██╗██╔════╝██╔══██╗
# █████╔╝ ██║     ██║██████╔╝██████╔╝█████╗  ██████╔╝
# ██╔═██╗ ██║     ██║██╔═══╝ ██╔═══╝ ██╔══╝  ██╔══██╗
# ██║  ██╗███████╗██║██║     ██║     ███████╗██║  ██║
# ╚═╝  ╚═╝╚══════╝╚═╝╚═╝     ╚═╝     ╚══════╝╚═╝  ╚═╝
#
# These supplemental settings essentially disable klipper's built in
# extrusion limits and is necessary when using an MMU
[extruder]
max_extrude_only_distance: 200
max_extrude_cross_section: 50

# For dialog prompts and progress in Mainsail. Requires Mainsail version >= v2.9.0
[respond]

# Other Happy Hare prerequisites. Harmless if already defined elsewhere in user config
[display_status]
[pause_resume]
[virtual_sdcard]
path: ~/printer_data/gcodes
#on_error_gcode: CANCEL_PRINT


# PRINT START/END ---------------------------------------------------------
# ██████╗ ██████╗ ██╗███╗   ██╗████████╗    ███████╗████████╗ █████╗ ██████╗ ████████╗
# ██╔══██╗██╔══██╗██║████╗  ██║╚══██╔══╝    ██╔════╝╚══██╔══╝██╔══██╗██╔══██╗╚══██╔══╝
# ██████╔╝██████╔╝██║██╔██╗ ██║   ██║       ███████╗   ██║   ███████║██████╔╝   ██║   
# ██╔═══╝ ██╔══██╗██║██║╚██╗██║   ██║       ╚════██║   ██║   ██╔══██║██╔══██╗   ██║   
# ██║     ██║  ██║██║██║ ╚████║   ██║       ███████║   ██║   ██║  ██║██║  ██║   ██║   
# ╚═╝     ╚═╝  ╚═╝╚═╝╚═╝  ╚═══╝   ╚═╝       ╚══════╝   ╚═╝   ╚═╝  ╚═╝╚═╝  ╚═╝   ╚═╝   
#   (base/mmu_software.cfg)
#
[gcode_macro _MMU_SOFTWARE_VARS]
description: Happy Hare optional configuration for print start/end checks
gcode: # Leave empty

# These variables control the behavior of the MMU_START_SETUP and MMU_START_LOAD_INITIAL_TOOL macros
variable_user_pre_initialize_extension      : '_CG28'	; Executed at start of MMU_START_SETUP. Commonly G28 to home
variable_home_mmu                           : False	; True/False, Whether to home mmu before print starts
variable_check_gates                        : True	; True/False, Whether to check filament is loaded in all gates used
variable_load_initial_tool                  : True	; True/False, Whether to automatically load initial tool
#
# Automapping strategy to apply slicer tool map to find matching MMU gate (will adjust tool-to-gate map). Options are:
#   'none'           - don't automap (i.e. don't update tool-to-gate map)
#   'filament_name'  - exactly match on case insensitive filament name
#   'material'       - exactly match on material
#   'color'          - exactly match on color (with same material)
#   'closest_color'  - match to closest available filament color (with same material)
#   'spool_id'       - exactly match on spool_id  [FUTURE]
variable_automap_strategy                   : "none"	; none|filament_name|material|color|closest_color|spool_id

# These variables control the behavior of the MMU_END macro
variable_user_print_end_extension           : ''	; Executed at start of MMU_END. Good place to move off print
variable_unload_tool                        : True	; True/False, Whether to unload the tool at the end of the print
variable_reset_ttg                          : False	; True/False, Whether reset TTG map at end of print
variable_dump_stats                         : True	; True/False, Whether to display print stats at end of print


# STATE MACHINE CHANGES ---------------------------------------------------
# ███████╗████████╗ █████╗ ████████╗███████╗     ██████╗██╗  ██╗ █████╗ ███╗   ██╗ ██████╗ ███████╗
# ██╔════╝╚══██╔══╝██╔══██╗╚══██╔══╝██╔════╝    ██╔════╝██║  ██║██╔══██╗████╗  ██║██╔════╝ ██╔════╝
# ███████╗   ██║   ███████║   ██║   █████╗      ██║     ███████║███████║██╔██╗ ██║██║  ███╗█████╗  
# ╚════██║   ██║   ██╔══██║   ██║   ██╔══╝      ██║     ██╔══██║██╔══██║██║╚██╗██║██║   ██║██╔══╝  
# ███████║   ██║   ██║  ██║   ██║   ███████╗    ╚██████╗██║  ██║██║  ██║██║ ╚████║╚██████╔╝███████╗
# ╚══════╝   ╚═╝   ╚═╝  ╚═╝   ╚═╝   ╚══════╝     ╚═════╝╚═╝  ╚═╝╚═╝  ╚═╝╚═╝  ╚═══╝ ╚═════╝ ╚══════╝
#   (base/mmu_state.cfg)
#
[gcode_macro _MMU_STATE_VARS]
description: Happy Hare configuration for state change hooks
gcode: # Leave empty

# You can extend functionality to all Happy Hare state change or event
# macros by adding a command (or call to your gcode macro).
# E.g for additional LED logic or consumption counters
variable_user_action_changed_extension      : ''	; Executed after default logic with duplicate params
variable_user_print_state_changed_extension : ''	; Executed after default logic with duplicate params
variable_user_mmu_event_extension           : ''	; Executed after default logic with duplicate params

# Maintenance warning limits (consumption counters)
variable_servo_down_limit                   : 5000      ; Set to -1 for no limit / disable warning
variable_cutter_blade_limit                 : 3000      ; Set to -1 for no limit / disable warning


# SEQUENCE MACRO - PARKING MOVEMENT AND TOOLCHANGE CONTROL ----------------
# ███╗   ███╗ ██████╗ ██╗   ██╗███████╗███╗   ███╗███████╗███╗   ██╗████████╗
# ████╗ ████║██╔═══██╗██║   ██║██╔════╝████╗ ████║██╔════╝████╗  ██║╚══██╔══╝
# ██╔████╔██║██║   ██║██║   ██║█████╗  ██╔████╔██║█████╗  ██╔██╗ ██║   ██║   
# ██║╚██╔╝██║██║   ██║╚██╗ ██╔╝██╔══╝  ██║╚██╔╝██║██╔══╝  ██║╚██╗██║   ██║   
# ██║ ╚═╝ ██║╚██████╔╝ ╚████╔╝ ███████╗██║ ╚═╝ ██║███████╗██║ ╚████║   ██║   
# ╚═╝     ╚═╝ ╚═════╝   ╚═══╝  ╚══════╝╚═╝     ╚═╝╚══════╝╚═╝  ╚═══╝   ╚═╝   
# Configure carefully if you 'enable_park: True'
#   (base/mmu_sequence.cfg)
#
[gcode_macro _MMU_SEQUENCE_VARS]
description: Happy Hare sequence macro configuration variables
gcode: # Leave empty
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

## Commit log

2025-01-11 First public release
    [Center_Drive_Roller_x4.stl, Foot_x4.stl, Idler_Roller_Axle_x4.stl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]
2025-01-11 add macro rewinder
    [rewinder_test.cfg]
2025-01-13 extruder update
    [extruder_mirror_x2.stl, extruder_motor_base_mirror_x2.stl, extruder_motor_base_x2.stl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]
2025-01-16 Update box and tensioner
    [[mmu]name_led.stl, [mmu]name_led_small.stl, box cover botton.stl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]
2025-01-31 Update new stls
    [Center_Drive_Roller_x4.stl, Idler_Roller_Axle_x4.stl, MMB_mount.stl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]
2025-01-31 Update new CAD
2025-03-09 Latch and Extruder Corrections
    [extruder_mirror_x2.stl, extruder_x2.stl, latch_mirror_x2.stl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]
2025-03-30 Updade config
    [mmu.cfg, mmu_button_eject.cfg, mmu_hardware.cfg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]
2025-04-02 fix encoder
    [[a]_Encoder_top.stl]
2025-05-17 update tools
    [Axle_Depth_Tool.stl]
2025-05-20 update wire size
    [LED_Soldering_Tool.stl, LED_Soldering_Tools.stl]
2025-05-28 Top mounting printer
    [250mm_mirror_x2.stl, 250mm_x2.stl, 300mm_mirror_x2.stl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]
2025-06-18 removed led soldering jig
2025-06-18 removed led welding template and updated ptfe tools
    [LED_Soldering_Tools.stl, PTFE_Tools.stl]
2025-06-23 Update CAD v1.2.2
2025-06-23 Manual Assembly v1.0
2026-02-16 update cad v2
2026-04-15 Release V2
    [250mm_mirror_x2.stl, 250mm_x2.stl, 2x_side_3mm.dxf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]
2026-04-16 Tensioner corrections
    [tensioner_arm_x4.stl]
2026-04-16 Update CAD
2026-04-16 Filename correction
    [[a]_monolith_mount_250_front_left.stl, [a]_monolith_mount_250_front_right.stl, [a]_monolith_mount_250_rear_left.stl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]
